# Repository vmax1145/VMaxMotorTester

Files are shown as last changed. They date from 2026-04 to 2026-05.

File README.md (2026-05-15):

# VMaxMotorTester DIY brushless motors thrust stand

## CAUTION !!! Be carefull when working with thrust stand. Rotating propeller is extreemly dangerous !!!  

Thrust stand is implemented with ESP32S3 supermini board to control Tekko32 F4 AM32 ESC 
and read extended KISS telemetry data as well as data from HX711 connected to load cell.
Collected data transmitted via USB serial to HTML page for visualization and control.
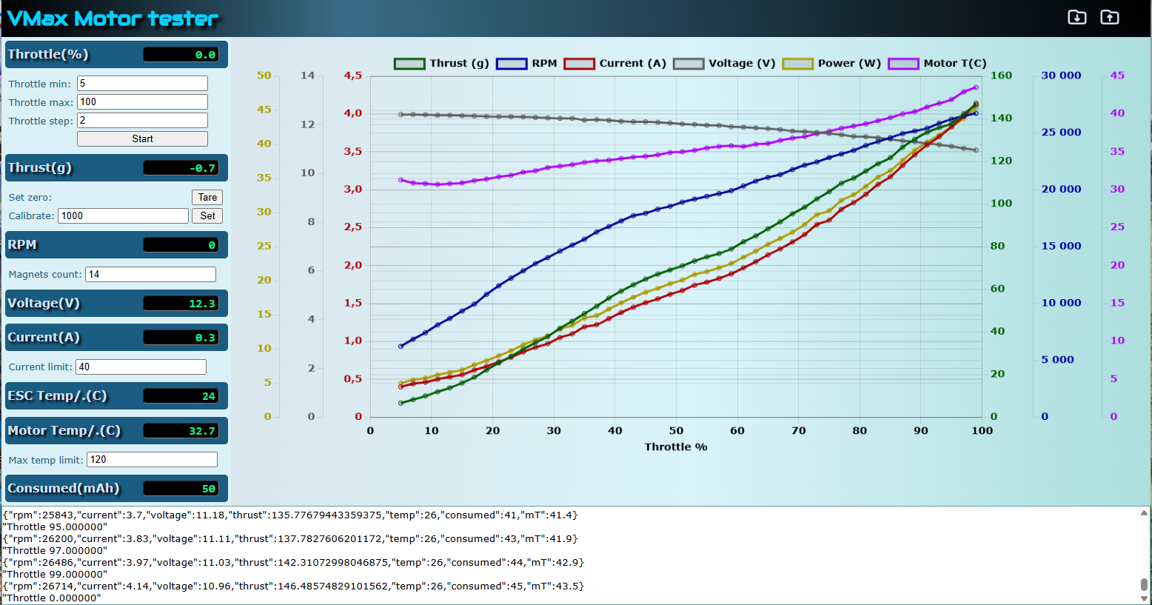
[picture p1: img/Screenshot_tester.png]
screenshot_tester


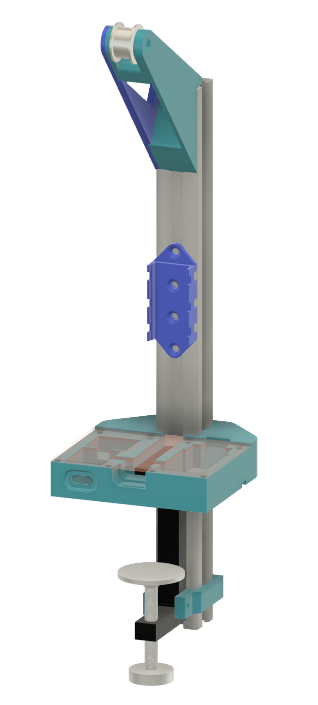
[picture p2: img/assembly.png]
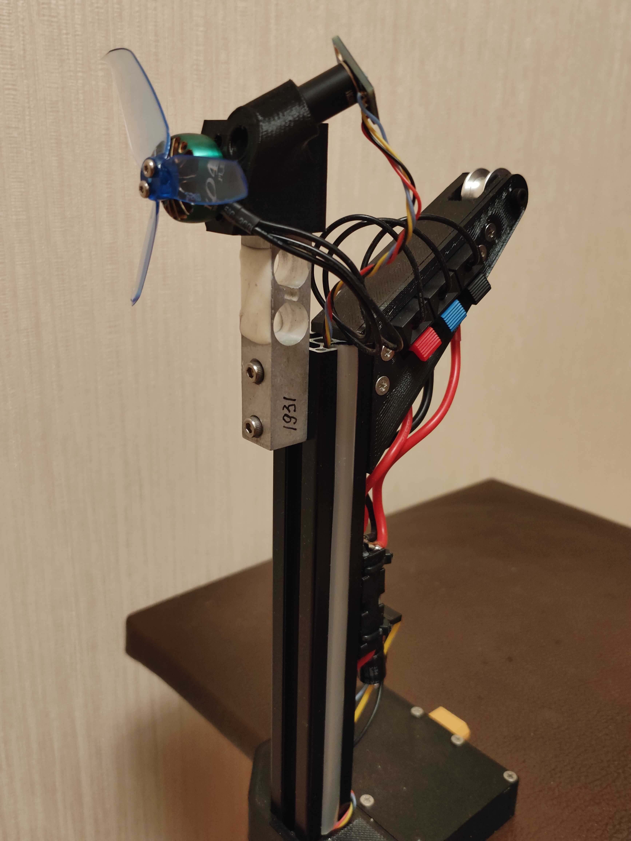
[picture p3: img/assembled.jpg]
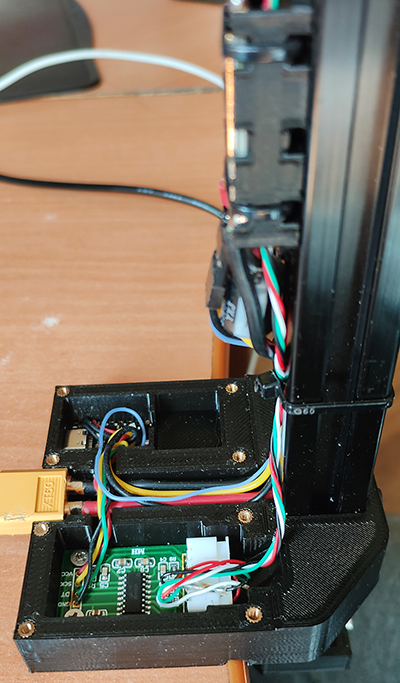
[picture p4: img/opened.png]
   

## Project include
- [Arduino sketch for ESP32S3 supermini board](arduino/README.md)
- [HTML application](html/README.md) (Chromium based browser required)
- STL files for 3d printed stand parts
- Autodesk Fusion360 3d model source file 

## Requirements
- Before wiring connect ESC to [AM32 configurator](https://am32.ca/configurator) and ensure 30ms telemetry on ESC telemetry output is enabled 
- Chromium based browser required to run HTML application.

## Wiring
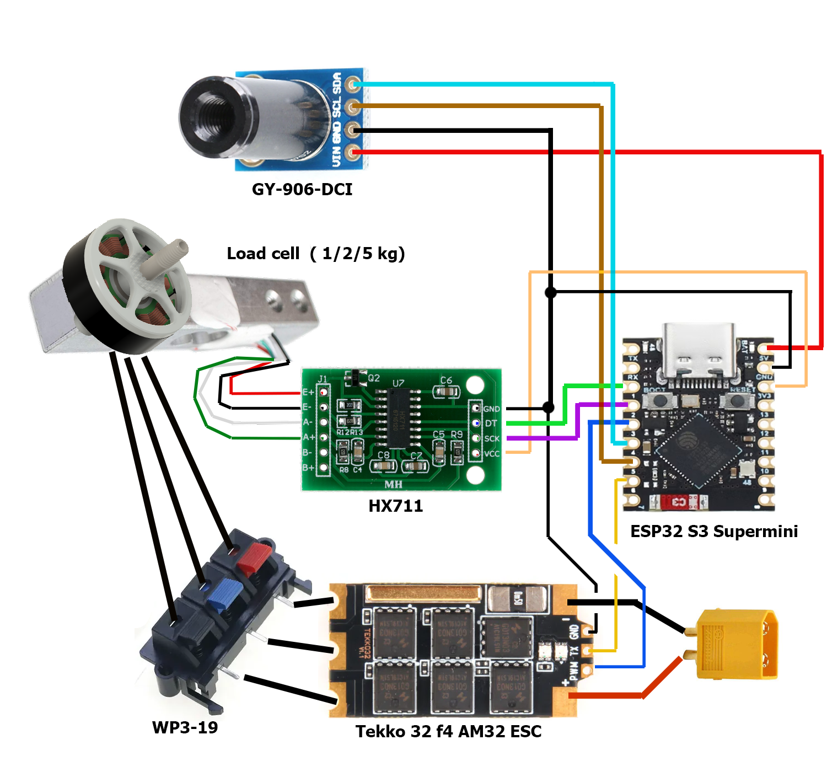
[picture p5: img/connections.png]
scheme


## Bill of materials
- [ESP32S3 supermini board](/img/esp32s3supermini.png)
- [HX711 amplifier and Load cell](/img/load_cell_HX711.png) Choose 1/2/5/10 KG load cell depending on your requirements. 
- [Tekko32 F4 AM32 ESC](/img/tekko32_bom.png) Or other ESC supporting full extended telemetry (erpm/temperature/current/voltage/consumption) on separate wire with KISS protocol.
- [Amass male XT60 connector](/img/xt60.jpg)
- [GT2 idler pulley 20T smooth, bore 3mm](/img/pulley.png) 
- [WP3-19 spring load connector](/img/WP3-19.png) Optional, but recommended.
- [2020 alluminium profile](/img/2020.png) 250-330mm length sutable for most cases up to 8-10 inch propellers. But for large propellers you may need more.
- [Clamp alluminium](/img/clamp.png) Printed parts are designed to match this specific clamp sizes
- [M2.5 inserts ⌀4mm l=5mm](/img/m3_inserts.png) (8 pcs)
- [M3 inserts ⌀4mm l=5mm](/img/m3_inserts.png) (2 pcs)
- [M3 profile nuts for 2020 profile](/img/M3_2020_nuts.png) (6pcs)
- AWG16 and AWG28 silicone wires
- M3, M2.5 bolts and nuts 
- [GY-906-DCI](/img/GY-906-2.png) IR temperature sensor (Optional)

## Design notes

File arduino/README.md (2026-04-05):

# Arduino HOWTO

### Installing ESP32 board manager
Open Arduino File->Preferences->Settings and add https://espressif.github.io/arduino-esp32/package_esp32_index.json
to Additional boards managerURLs  

### Installing required libraries 
Click on Library icon and add the following libraris   
 - Arduino_JSON by Arduino (version 0.2.0)
 - DShotRMT by Wastl Kraus  (version 0.2.0)
 - HX711 by Rob Tillaart  (version 0.6.3)
 - Preferences by Volodymyr Shymanskyy (version 2.2.2)
 - Simple Web Serial by Fabian Mohr  (version 1.0.0)

### Select board and port 
For ESP32S3 supermini open Select Board and Port dialog and search for
'esp32s3 dev module'. Connect USB cable and select COM port.   

### Tools settings
Just for info screenshot with settings in tools menu 
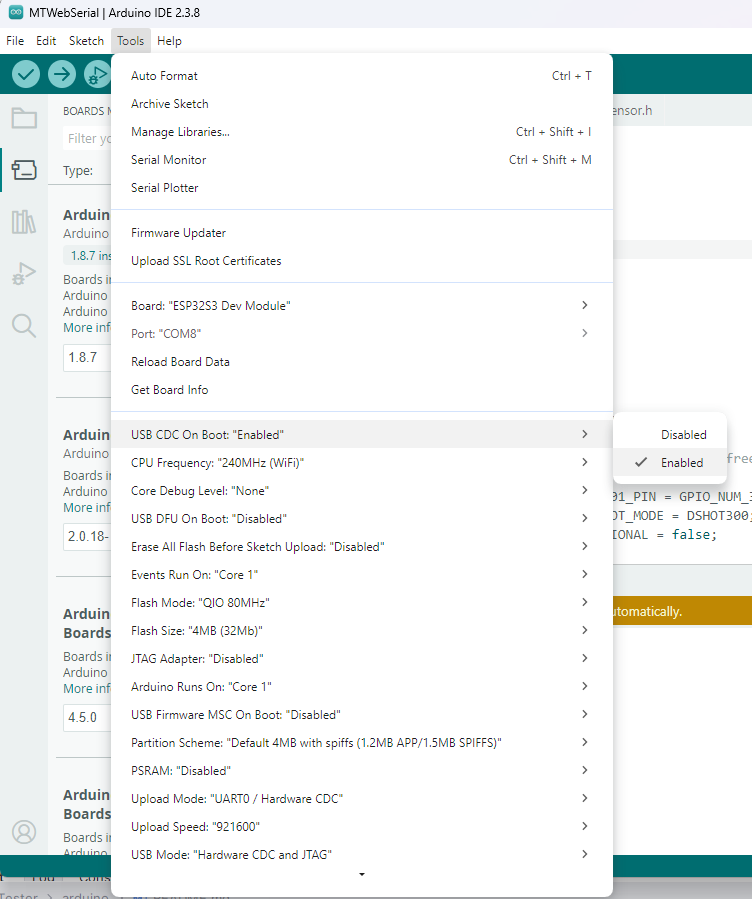
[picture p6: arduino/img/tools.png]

 
### Sketch tuning 
One can change defaults in [MTWebSerial.ino](MTWebSerial/MTWebSerial.ino) 
including pin assignments and default scale calibration coefficient
```c++
#define HX711_DATA_PIN 1
#define HX711_CLK_PIN 2
#define THRUST_SCALE_DEFAULT  1931.0
#define TELEMETRY_RX_PIN GPIO_NUM_6
#define TELEMETRY_TX_PIN GPIO_NUM_7 //dummy any free pin
```
NOTE: Changes of scale calibration coefficient requires reflashing with full flash erasing   
otherwise value stored in preferences will be used instead

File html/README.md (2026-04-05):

# HTML Application for [VmaxMotorTester project](../) 

## CAUTION !!! Be carefull when working with thrust stand. 
## Rotating propeller is extreemly dangerous !!!
## Connect power battery just before starting test and disconnect after test end.   

### Features
 - Automatically detect motor rotation direction and reverse it when necessary 
 - Measure sweeping throttle from defined min to defined max values
 - Display charts for thrust, RPM, current, voltage and power 
 - Save and load measured data to file
 
screenshot_tester

### Chrominum based browser required to run application
Modern WebSerialApi is essential for connectivity between motor tester stand and browser HTML application via USB.
This API is only supported in chromium based browsers like  
Google Chrome, Microsoft Edge, Opera, Brave browsers.
Please, choose right browser to run application.

### Load cell Calibration instructions.
SAFETY FIRST!!! DISCONNECT BATTERY POWER. 

Tie a thin nylon cord to the load cell exactly at the motor axis level 
(in the middle between 2 mount holes) and 
put free end of cord over pulley. 

Connect USB cable and start application.
Without any load on cord free end press 'Tare' button.
Wait 2-3 seconds... Measured weight must go to Zero.  
Next step - tie a known weight ( 1000 gramm for example ) to the free end of cord.
Enter this known weight value in 'Calibration' input field and press 'Set' button.
Now measured weight must be shown same as you entered (almost same) 
You are done.  
Remove calibration weight and cord to avoid getting hit by a spinning propeller during tests

Calibration coefficient is stored in ESP32 flash memory 
so you do not need to do this each time...

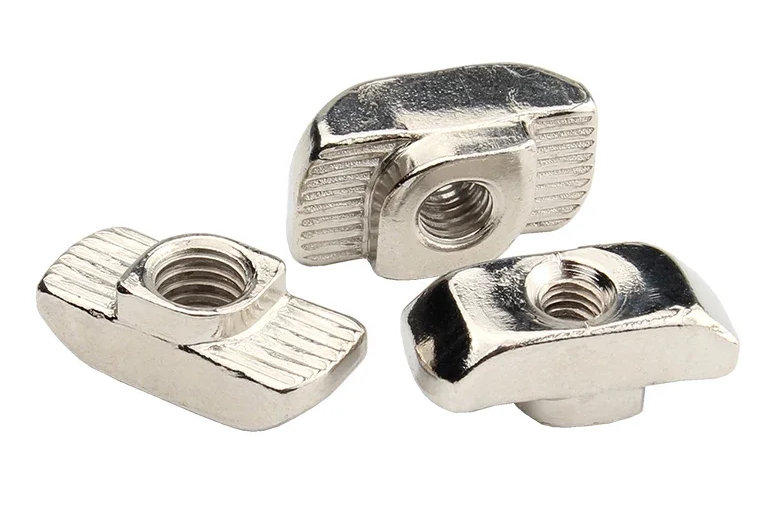
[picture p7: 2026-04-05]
img/M3_2020_nuts.png

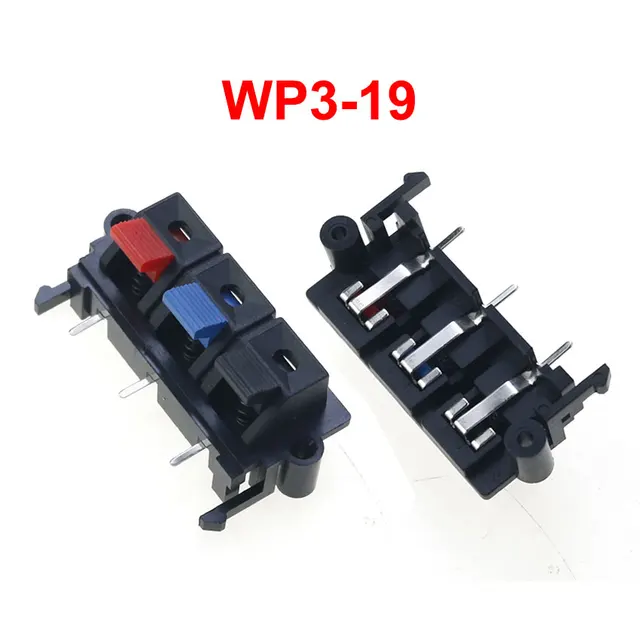
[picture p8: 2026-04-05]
img/WP3-19.png

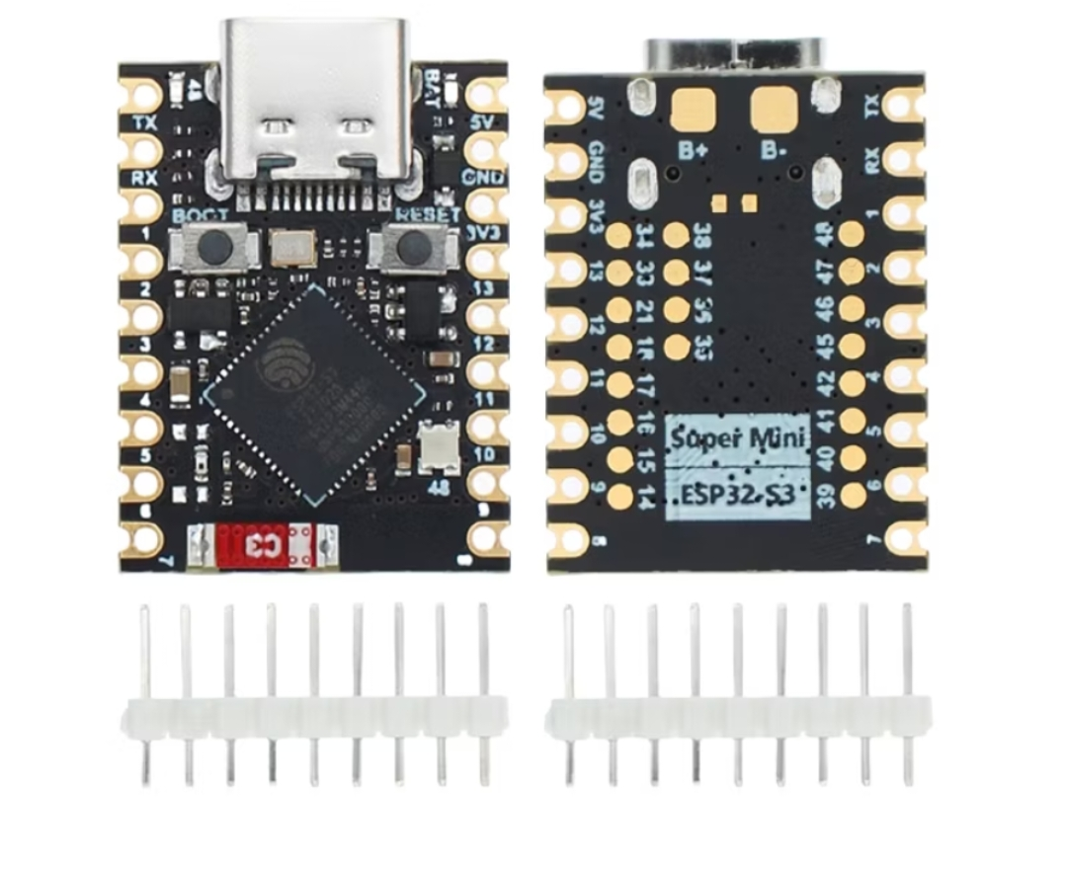
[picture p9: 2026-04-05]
img/esp32s3supermini.png

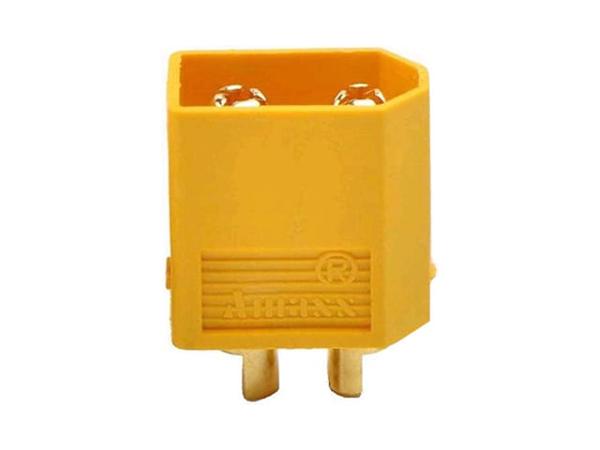
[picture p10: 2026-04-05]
img/xt60.jpg

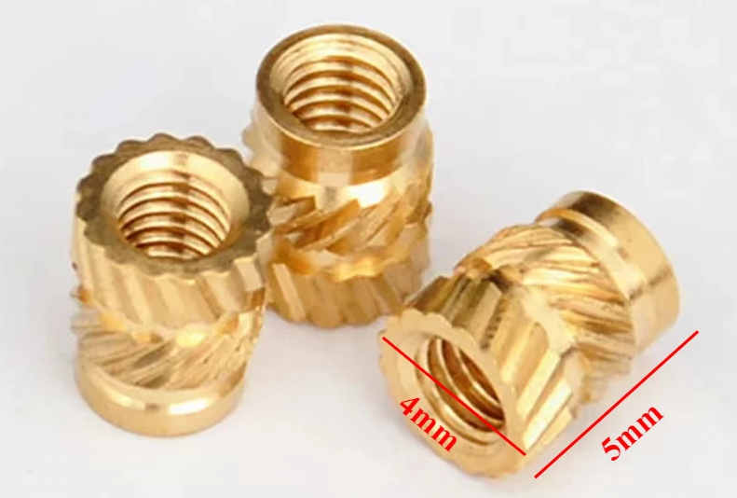
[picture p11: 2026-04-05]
img/m3_inserts.png

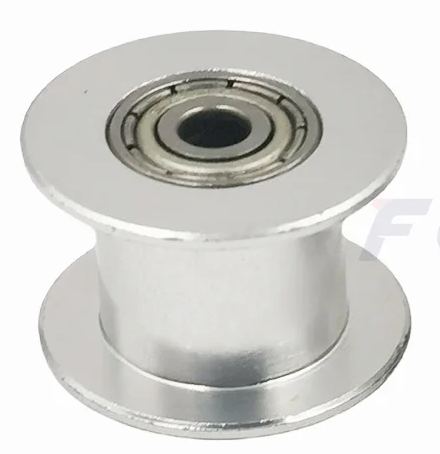
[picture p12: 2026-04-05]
img/pulley.png

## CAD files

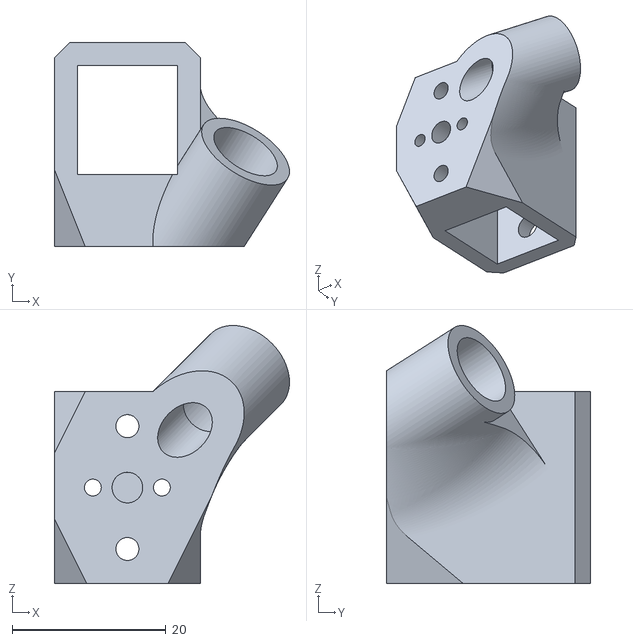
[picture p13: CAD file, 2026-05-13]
stl/mot_adapter.stl
30.6 x 26.6 x 33.6

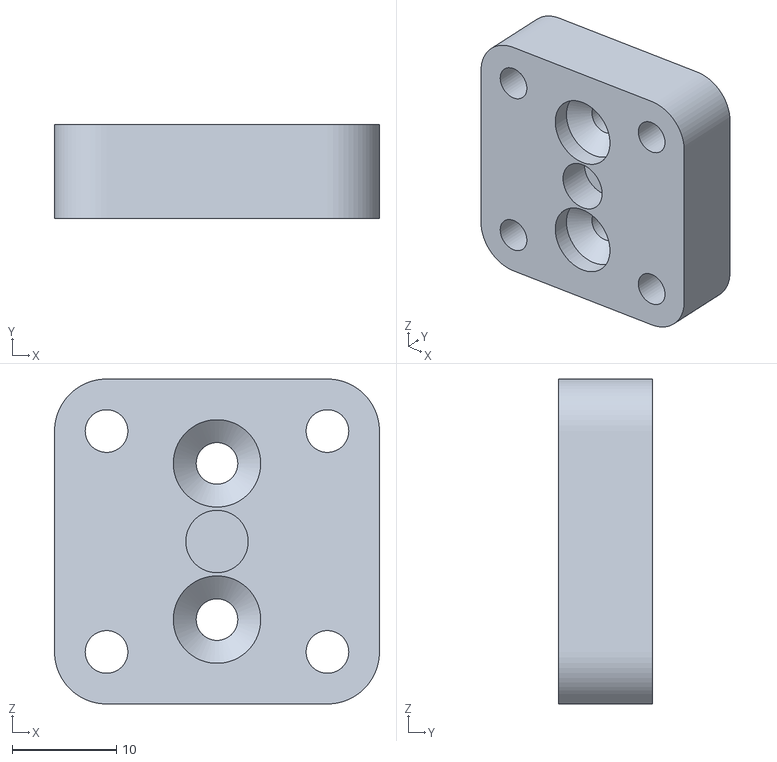
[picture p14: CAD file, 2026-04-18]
stl/mot_adapter_30.stl
31.2 x 9.00 x 31.2

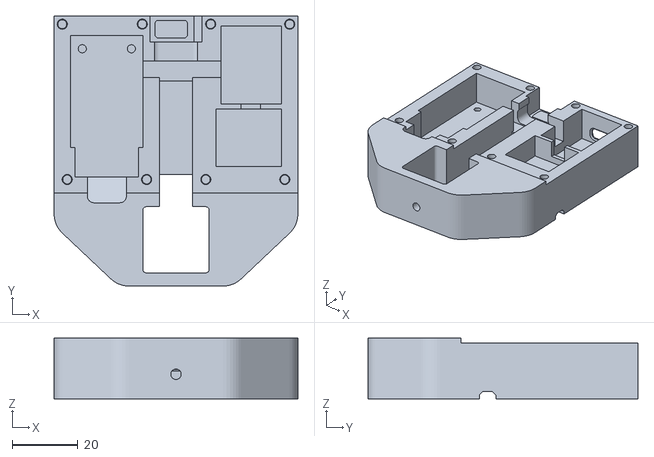
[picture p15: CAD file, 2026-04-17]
stl/clam_top2_m.stl
74.4 x 82.4 x 18.5

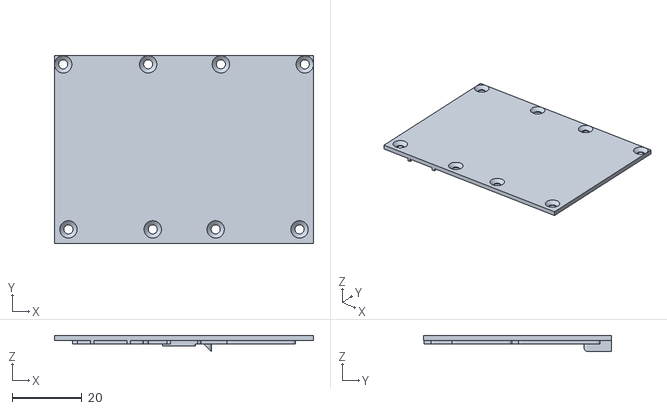
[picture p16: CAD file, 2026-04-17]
stl/clam_top2_c.stl
74.4 x 53.9 x 4.62

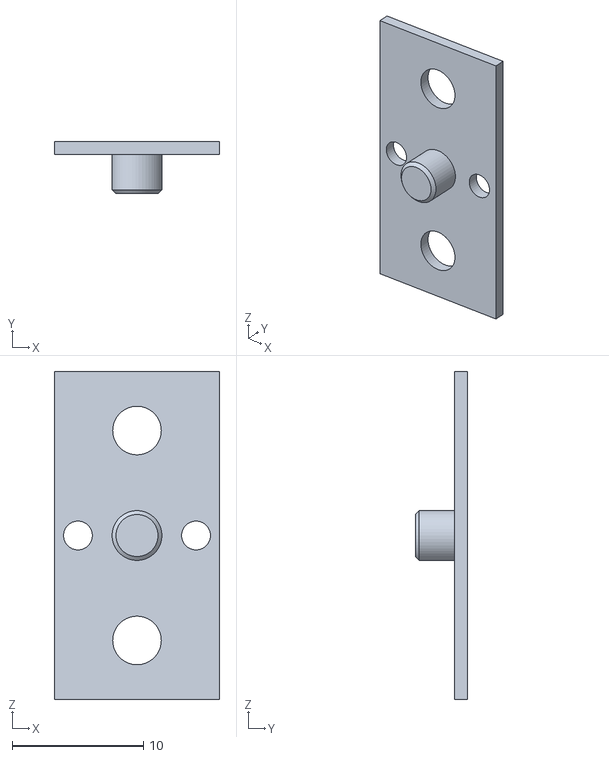
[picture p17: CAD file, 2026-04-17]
stl/mot_fixer.stl
12.6 x 4.00 x 25.0

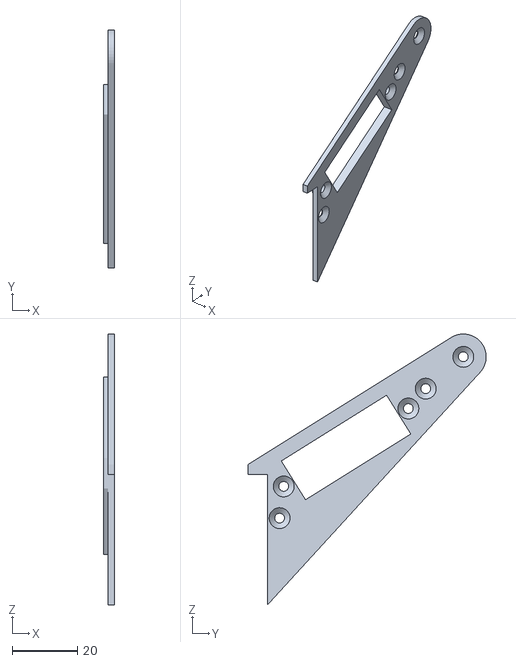
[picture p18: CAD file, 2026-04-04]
stl/scale_arm_c.stl
3.50 x 73.0 x 83.0

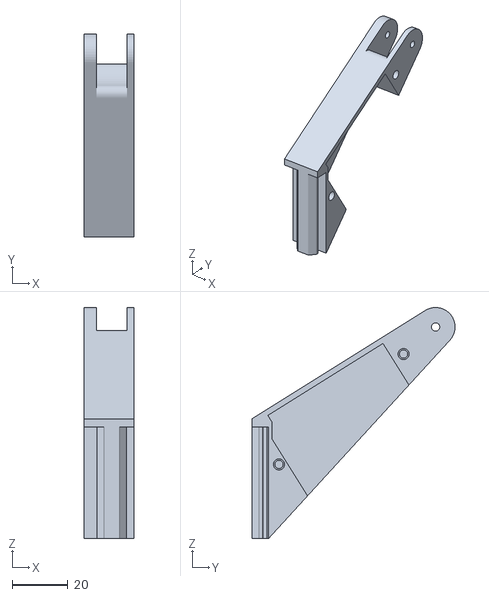
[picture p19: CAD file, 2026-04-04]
stl/scale_arm_m.stl
18.0 x 73.0 x 83.0

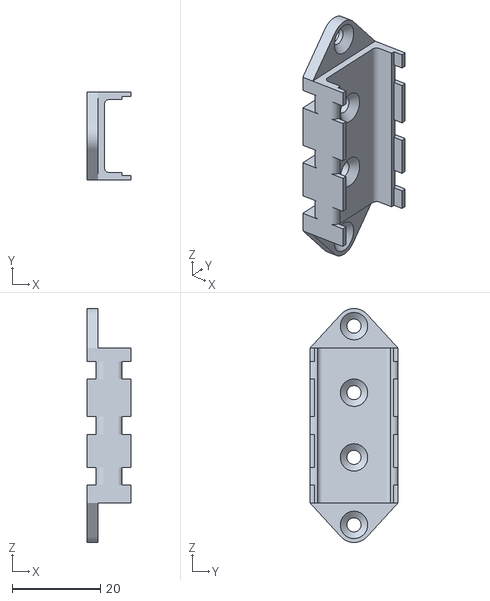
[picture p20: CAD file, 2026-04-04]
stl/esc_mnt.stl
10.0 x 20.0 x 53.0

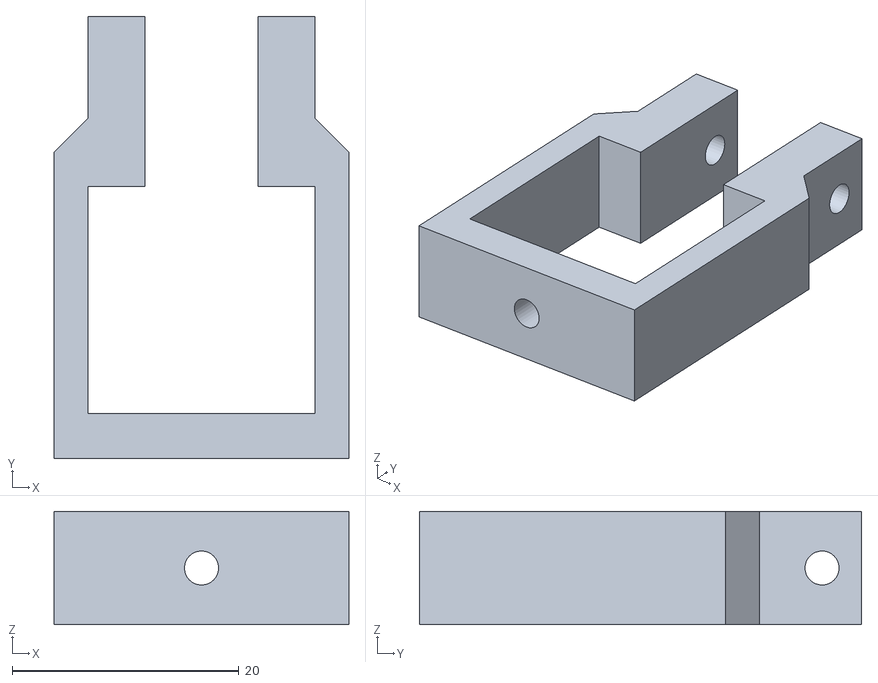
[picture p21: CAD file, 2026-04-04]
stl/clamp_bottom.stl
26.0 x 39.0 x 10.0

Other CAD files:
fusion360/MotorTester.f3d

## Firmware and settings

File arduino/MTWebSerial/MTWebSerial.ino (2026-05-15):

#include <Constants.h>
#include <HX711.h>
#include <DShotRMT.h>
#include "Thrust_sensor.h"
#include <Arduino_JSON.h>
#include <SimpleWebSerial.h>
#include <Wire.h>
#include <Adafruit_MLX90614.h>



SimpleWebSerial WebSerial;
JSONVar readings;

ThrustSensor thrustSensor;

/*
ESP32 S3 Supermini 
Safe to use pins
IO1
IO2
IO4
IO5
IO6
IO7
IO8
IO15
IO16
IO17
IO18
IO21

Pins to use with cautions
IO3	GPIO3	Sampled at reset to select JTAG interface (USB Serial/JTAG controller vs. external pins). Improper use can disable external JTAG or alter debug interface.	🛠️ Strapping
IO9	FSPIHD	Connected to external flash (data/hold signal) on most modules. Not recommended for use as GPIO, since it must remain dedicated to flash communication.	⚡ Flash
IO10	FSPICS0	Used to select the external flash chip. It is required for flash access and cannot be repurposed without losing flash connectivity	⚡ Flash
IO11	FSPID	Used as a data line for flash (and in-package PSRAM). It should not be used as GPIO when the flash/PSRAM is in use.	⚡ Flash
IO12	FSPICLK	Drives the flash (and PSRAM) clock. This critical signal must be reserved for memory and not used as general GPIO.	⚡ Flash
*/



#define HX711_DATA_PIN 1
#define HX711_CLK_PIN 2
#define MOTOR01_PIN GPIO_NUM_3 // unsafe pin?
#define GY906_DATA GPIO_NUM_4
#define GY906_CLK GPIO_NUM_5
#define TELEMETRY_RX_PIN GPIO_NUM_6
#define TELEMETRY_TX_PIN GPIO_NUM_7 //dummy any free pin


//static constexpr gpio_num_t MOTOR01_PIN = GPIO_NUM_3;
static constexpr dshot_mode_t DSHOT_MODE = DSHOT300;
static constexpr auto IS_BIDIRECTIONAL = false;

#define THRUST_SCALE_DEFAULT  1931.0

#define MLX90614_I2C_ADRR 0x5a

static uint16_t throttle = DSHOT_CMD_MOTOR_STOP;

unsigned long lastTime = 0;
unsigned long timerDelay = 200;
static int16_t step = 0;

bool mlxFound = false;


char termbuff[64];
static uint8_t telemetryBuff[10];

volatile uint8_t measureInx=0;
volatile uint16_t temperature[4] ={0,0,0,0};
volatile uint16_t voltage[4] = {0,0,0,0};
volatile uint16_t current[4] = {0,0,0,0};
volatile uint16_t consumed[4] = {0,0,0,0}; // used mA/h
volatile uint16_t erpm[4] = {0,0,0,0};


DShotRMT motor01(MOTOR01_PIN, DSHOT_MODE, IS_BIDIRECTIONAL);
Adafruit_MLX90614 mlx = Adafruit_MLX90614();
int16_t motTemp = -255;
int16_t ambTemp = -255;

uint16_t avgMeasure(volatile uint16_t *measureData) {
    uint16_t ret = 0;
    for(uint8_t i=0;i<4;i++) {
        ret+=measureData[i];
    }
    return ret/4;
}


float prevThrust = 0;
JSONVar getSensorReadings(){
    float thrust = thrustSensor.measure();
    readings["thrust"]  =  (prevThrust+thrust)/2.0;
    prevThrust = thrust;
    readings["voltage"] = avgMeasure(voltage);
    readings["current"] = avgMeasure(current);
    readings["erpm"] = avgMeasure(erpm);
    readings["temp"] = avgMeasure(temperature);
    readings["consumed"] = avgMeasure(consumed);
    if(mlxFound) {
        readings["mT"] = motTemp;
        readings["aT"] = ambTemp;
    }
    return readings;
}


void parseCommand(JSONVar myObject) {    

    if(JSON.typeof(myObject) == "undefined") {
        WebSerial.send("term","undefined command");
    }
    else{
        if(myObject.hasOwnProperty("tare")) {
            thrustSensor.zero();
            WebSerial.send("term","Thrust zero set");
        }
        if(myObject.hasOwnProperty("thrust")) {
            double v= (double)(myObject["thrust"]);
            float_t val = float(v);
            thrustSensor.calibrateScale(val);            
            sprintf(termbuff, "Thrust set at %i", val);
            WebSerial.send("term",termbuff);
        }
        if(myObject.hasOwnProperty("throttle")) {                        
            double v= (double)(myObject["throttle"]);
            if(v==0) {
               throttle=0;
            }
            else {
               throttle = DSHOT_THROTTLE_MIN + v*(DSHOT_THROTTLE_MAX-DSHOT_THROTTLE_MIN)/100;
            }            
            sprintf(termbuff, "Throttle %f", v);
            WebSerial.send("term",termbuff);
        }
        if(myObject.hasOwnProperty("spin")) {            
            bool v = ((int)(myObject["spin"]))>0;            
            
            motor01.sendCustomCommand(DSHOT_CMD_MOTOR_STOP, 10, 1000);            
            motor01.sendCustomCommand(v ? DSHOT_CMD_SPIN_DIRECTION_NORMAL : DSHOT_CMD_SPIN_DIRECTION_REVERSED, 10, 1000);            
            motor01.sendCustomCommand(DSHOT_CMD_SAVE_SETTINGS, 10, 1000);            
            sprintf(termbuff, "Spin dir %s", v ? "forward":"reversed");
            WebSerial.send("term",termbuff);
        }
        if(myObject.hasOwnProperty("echo")) {
            String v = (String)(myObject["echo"]);
            WebSerial.send("term","ECHO:"+v);
        }
    }
}


uint8_t update_crc8(uint8_t crc, uint8_t crc_seed){
	uint8_t crc_u, i;
	crc_u = crc;
	crc_u ^= crc_seed;
	for ( i=0; i<8; i++) crc_u = ( crc_u & 0x80 ) ? 0x7 ^ ( crc_u << 1 ) : ( crc_u << 1 );
	return (crc_u);
}

uint8_t get_crc8(uint8_t *Buf, uint8_t BufLen) {
	uint8_t crc = 0, i;
	for( i=0; i<BufLen; i++) crc = update_crc8(Buf[i], crc);
	return (crc);
}

void onKiss() {
    uint8_t receivedCnt = Serial1.available();
    if(receivedCnt != 10) {
        while(receivedCnt > 0) {
            Serial1.read();
            receivedCnt--;
        }
        return;
    }
    else {
        Serial1.read(telemetryBuff,10);
        uint8_t crc8 = get_crc8(telemetryBuff, 9); // get the 8 bit CRC
        if(crc8 != telemetryBuff[9]) {
            return;
        }
        temperature[measureInx] = telemetryBuff[0]; // temperature
        voltage[measureInx] = (telemetryBuff[1]<<8)|telemetryBuff[2]; // voltage        
        current[measureInx] = (telemetryBuff[3]<<8)|telemetryBuff[4]; // Current
        consumed[measureInx] = (telemetryBuff[5]<<8)|telemetryBuff[6]; // used mA/h
        erpm[measureInx] = (telemetryBuff[7]<<8)|telemetryBuff[8]; // eRpM *100
        measureInx = (measureInx+1)%4;
    }
}

void setup() {
   Serial.begin(115200);

   WebSerial.on("cmd", parseCommand);  
   thrustSensor.begin(HX711_DATA_PIN,HX711_CLK_PIN, THRUST_SCALE_DEFAULT);
   motor01.begin();

   Serial1.begin(115200,SERIAL_8N1,TELEMETRY_RX_PIN,TELEMETRY_TX_PIN);
   Serial1.setRxTimeout(5);
   Serial1.onReceive(onKiss,false);

   Wire.begin(GY906_DATA, GY906_CLK);
   if (mlx.begin(MLX90614_I2C_ADRR, &Wire) ) {
       mlxFound = true;
   };
}




void loop() {
    unsigned long delta = millis() - lastTime; 
        
    WebSerial.check();
    motor01.sendThrottle(throttle);

    if(mlxFound){        
        if(step==1) {
            motTemp = mlx.readObjectTempC()*10.0;
        }
        else if(step==2) {
            ambTemp = mlx.readAmbientTempC()*10.0;
        }
    }
    step++;
    if (delta > timerDelay) {              
       JSONVar sensorReadings = getSensorReadings();
       WebSerial.send("value", sensorReadings);       
       lastTime = millis();                      
       step = 0;
    }
}

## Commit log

2026-04-05 break check direction on 40% throttle
2026-04-05 edit readme
    [MotorTester.f3d]
2026-04-17 add motor adapters
    [MotorTester.f3d, clam_top2_c.stl, mot_adapter.stl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]
2026-04-18 fix connections drawing
    [MotorTester.f3d, mot_adapter_30.stl]
2026-05-13 add GY-906 IR temperature sensor
    [MotorTester.f3d, mot_adapter.stl]
2026-05-14 Add motor temperature limit
2026-05-15 fix connections img, add GY-906-DCI
    [MTWebSerial.ino]
